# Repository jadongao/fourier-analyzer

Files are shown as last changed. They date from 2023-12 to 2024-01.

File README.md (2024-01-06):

# LEGO Fourier Analyzer
A LEGO machine that presents Fourier Analysis 

GitHub Link: (https://github.com/jadongao/fourier-analyzer)

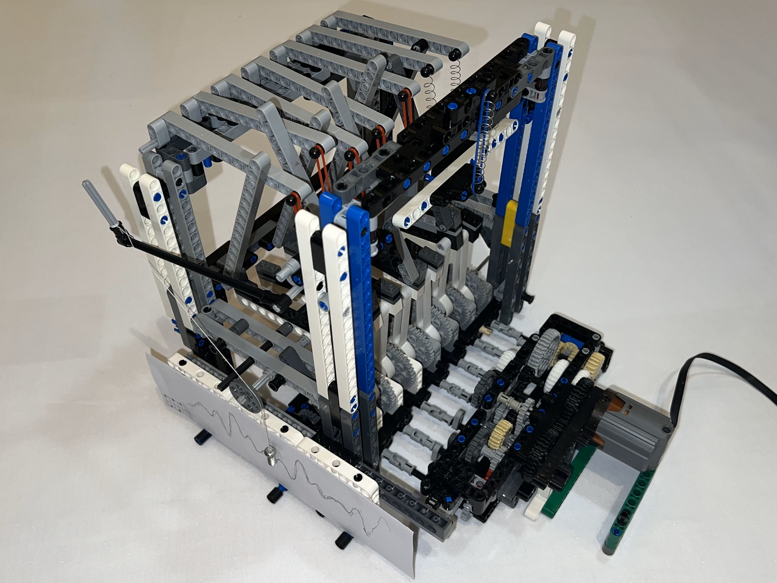
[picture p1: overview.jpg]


# 1. What kind of thing is this work?

I made a LEGO machine that presents Fourier Analysis in a highly visual way. This machine replicates a Harmonic Analyzer designed in the late nineteenth century by the physicist Albert Michelson. I must clarify that I referred to the video of YouTuber @thoroughfareproduction, who created a 5-element analyzer. I redesigned the gearbox to increase the number of elements to 7 and made improvements in the design of the sinusoid generator gear set to make the operation smoother.

# 2. How to characterize/categorize this work?

LEGO machine, Fourier Analysis, Sinusoid, 3D models, Visual Learning

# 3. Briefly description of this work

A Fourier analyzer can carry out two related tasks: add weighted sines or cosines to produce a function graph and perform the inverse operation of decomposing a given function graph into its constituent sinusoids. The addition of sinusoids is called Fourier synthesis, and the inverse operation is called Fourier Analysis. This type of machine is an analog computer that directly processes function graphs without the digital computer, which is almost considered essential by people today. It does not require electricity and can be operated by hand.

The capability of the Fourier analyzer depends on the number of elements. I tried to increase the number of elements to 7, while Albert Michelson's copper analyzer once achieved 80 elements.

## Example of Fourier analysis

Taking Fourier synthesis (5 sinusoids element) as an example,

<!--![sinusoid function graph of computer](./computer%20function%20graph.jpg) -->
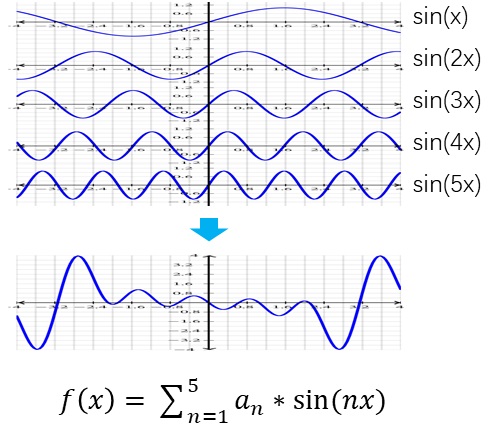
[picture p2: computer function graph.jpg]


where $a_n$ is -1, +1, -1, +1, -1

F (x)= -sin(x)+sin(2x)-sin(3x)+sin(4x)-sin(5x)

Using this LEGO Fourier Analyzer, the output function graph is as follows, which is very close to the graph drawn by the computer.

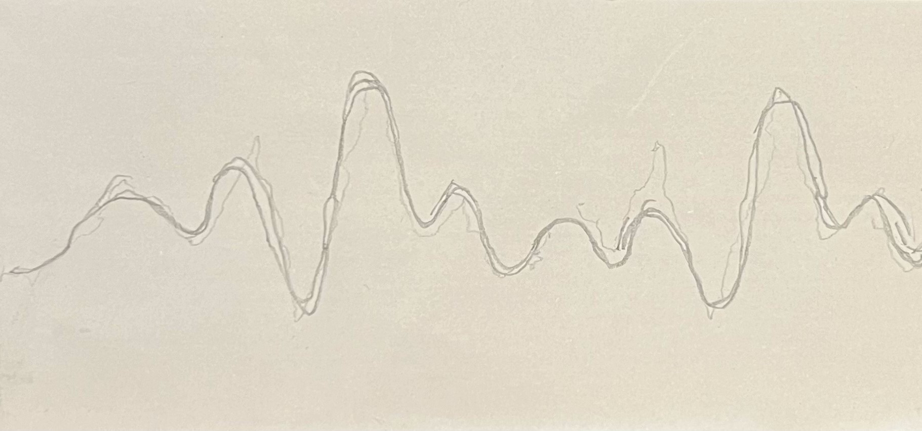
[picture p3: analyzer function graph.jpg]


## Parts of analyzer
This LEGO machine consists of the following parts:

<!--![parts of Analyzer](./overview%20with%20label.jpg)  -->
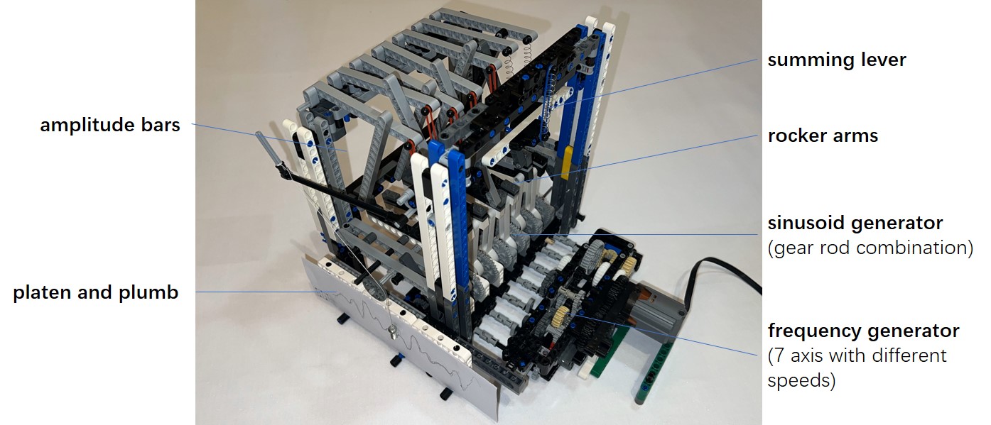
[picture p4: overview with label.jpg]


### 3.1 Frequency generator
The frequency generator is a gearbox with seven output shafts of different frequencies. The rotational speeds on the seven axes are 1x, 2x, 3x, 4x, 5x, 6x, and 7x, respectively.

### 3.2 Sinusoid generator
The sinusoid generator has seven gears to move Rocker arms, converting the circular rotation generated by the frequency generator into sinusoidal motion. This combination of mechanical elements produces the seven different sinusoidal waves: sin(1x), sin(2x), sin(3x), sin(4x), sin(5x), sin(6x), and sin(7x).

### 3.3 Ample bars, weight the sinusoids
There are 7 sinusoidal motions weighted: $a_1$*sin(1x), $a_2$*sin(2x), $a_3$*sin(3x), $a_4$*sin(4x), $a_5$*sin(5x), $a_6$*sin(6x), and $a_7$*sin(7x).
### 3.4 Summing lever
The summing lever at the top of the machine adds together the weighted sinusoids.

### 3.5 Platen and Plumb
The platen moves horizontally, and the plumb moves vertically. The pen tied to the plumb draws a function graph of the calculation result on the recording paper.

# 4. How do I make it?
Since March 2022, I have been in contact with the Harmonic Analyzer, designed by physicist Albert Michelson for studying calculus and Fourier transform, and its clever design has deeply impressed me. So I wanted to make one myself at home. The entire process took considerable time and effort to complete each component.

The sinusoid generator and frequency generator are two essential parts:

### Frequency generator
The frequency generator is a gearbox, and I am amazed by the clever design of Youtuber @thoroughfareproduction. However, because this YouTuber only provided videos without detailed installation drawings, I couldn't see his internal structure and had to explore it myself. I first completed a 5-axis gearbox like a YouTuber's machine, and after finishing it, my confidence doubled. I challenged and assembled a 7-axis gearbox.

<!--![gear set](./frequency%20generator%20gear%20set.jpg) -->
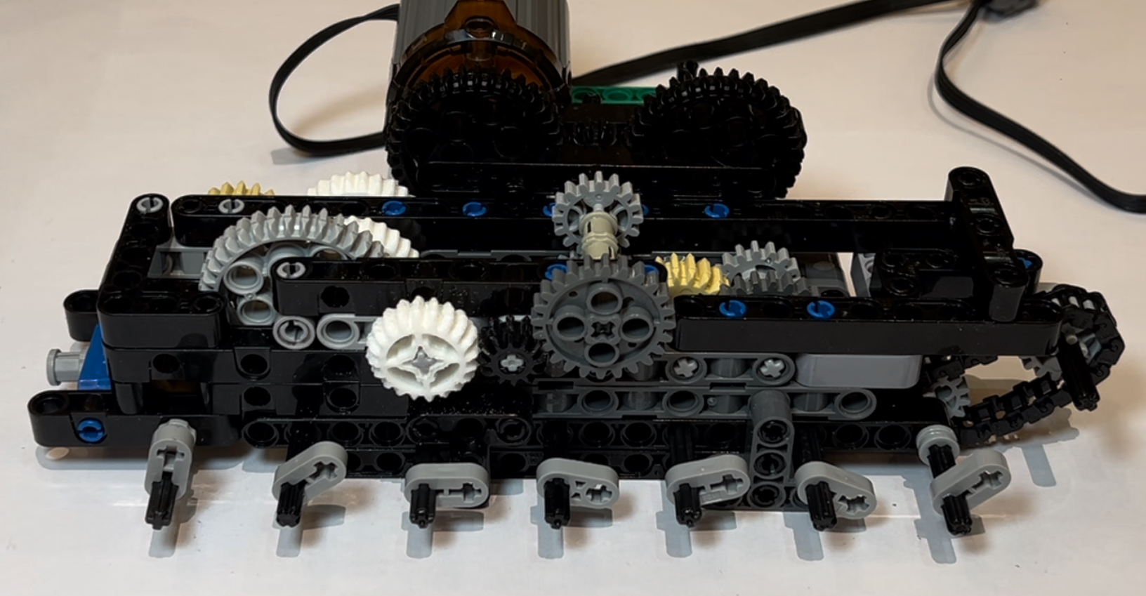
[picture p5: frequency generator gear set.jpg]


This machine uses almost all LEGO gears: 8, 12, 16, 20, 24, 28, and 36 teeth gear. Since I don't have all gear types at home, I temporarily used a 3D printer to print several types. Later, I replaced the 3D-printed parts with purchased LEGO parts, which made the operation more stable. This method of testing before formal procurement dramatically improves production efficiency, eliminating the need to wait several days to receive LEGO parts before testing.

### Sinusoid generator
The sinusoid generator uses LEGO worm gear to transmit circumferential rotation, but during the manufacturing process, there was a problem. Due to the fixed position of the gears and worm, the worm would get stuck during operation, and the entire device could not operate then. I had to take a break until a few months later when I had time to conduct many repeated experiments and finally found a solution. The final method found is straightforward: to make the worm position lose to avoid jamming. But to see this method, I should do many repeated disassembly and assembly. 

The device that drives the LEGO beam to form sinusoidal motion is crucial. Youtuber @thoroughfareproduction used a simple bolt connection, but the bolt connection was loose due to the need for rotation, which caused the gears and beam to shake often. I made improvements using a 3D-printed model and bearings, and it is no longer a classic LEGO work.

<!--![gear-rod and bearing](./gear-rod%20and%20bearing%20with%20label.jpg)-->
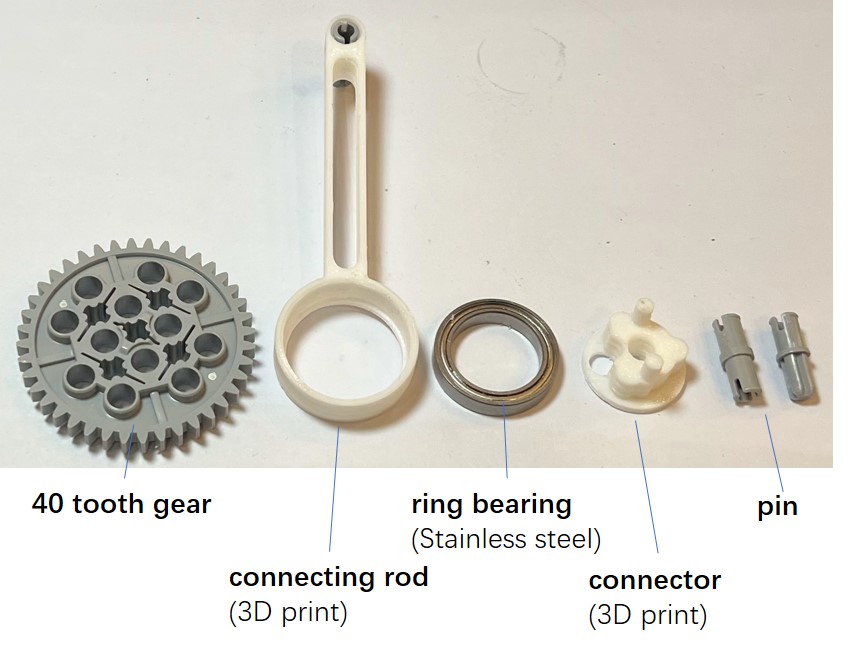
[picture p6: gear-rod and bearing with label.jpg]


<!--![sinusoid generator](./sinusoid%20generator%20gear-rod.jpg) -->
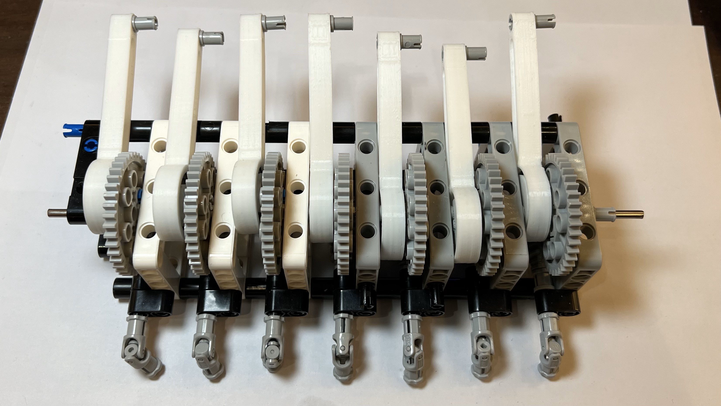
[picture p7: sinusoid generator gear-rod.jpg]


# 5. Why do I make it?

When learning sound waves, I came across the idea that chords are composed of different combinations of sounds, and using Fourier Analysis, chords can be decomposed into the frequencies of their constituent sounds. I am very interested in Fourier Analysis, and I saw videos online from Professor Bill Hammack and YouTuber @thoroughfareproduction, both dedicated to visualizing complex mathematical concepts in Fourier Analysis. So, I decided to learn from them and make a LEGO machine myself. When making this machine, I also traced the history of Fourier Analysis. I had a chance to communicate with these masters during this production process, and I felt their imaginative ideas in the era without electronic computers.

<table border="0">
 <tr>
    <td><b style="font-size:30px">Time</b></td>
    <td><b style="font-size:30px">Name</b></td>
    <td><b style="font-size:30px">Invention</b></td>
 </tr>
 <tr>
    <td>1807</td>
    <td>French mathematician and physicist Fourier </td>
    <td>He published a paper that used sine curves to describe temperature distribution: periodic functions can be represented by a series of cosines and sines.</td>
 </tr>
<tr>
    <td>1879</td>
    <td>Sir William Thomson (Lord Kelvin)</td>
    <td>He designed a 15 constituent sinusoids tide predicting machine (TPM). </td>
</tr>
<tr>
    <td>1898</td>
    <td>Physicist Albert Michelson (Nobel Prize Winner) </td>
    <td>He designed the Harmonic Analyzer that calculates with 20 sinusoids. </td>
</tr>
<tr>
    <td>November 12, 2014</td>
    <td>Professor Bill Hammack </td>
    <td>He uses videos and PDF books to introduce Albert Michelson's Harmonic Analyzer. </td>
</tr>
<tr>
    <td>August 19, 2021</td>
    <td>Youtuber @thoroughfareproduction </td>
    <td>They designed a wondrous LEGO contraption of gears, springs, levers, and wheels to perform Fourier analysis. </td>
</tr>
</table>

# 6. What's the most meaningful thing you've made?

This LEGO machine can correspond one-to-one with mathematical formulas, which visualizes mathematical concepts and helps me understand them.

<!--![sinusoid generator](./math%20to%20machine.jpg)-->
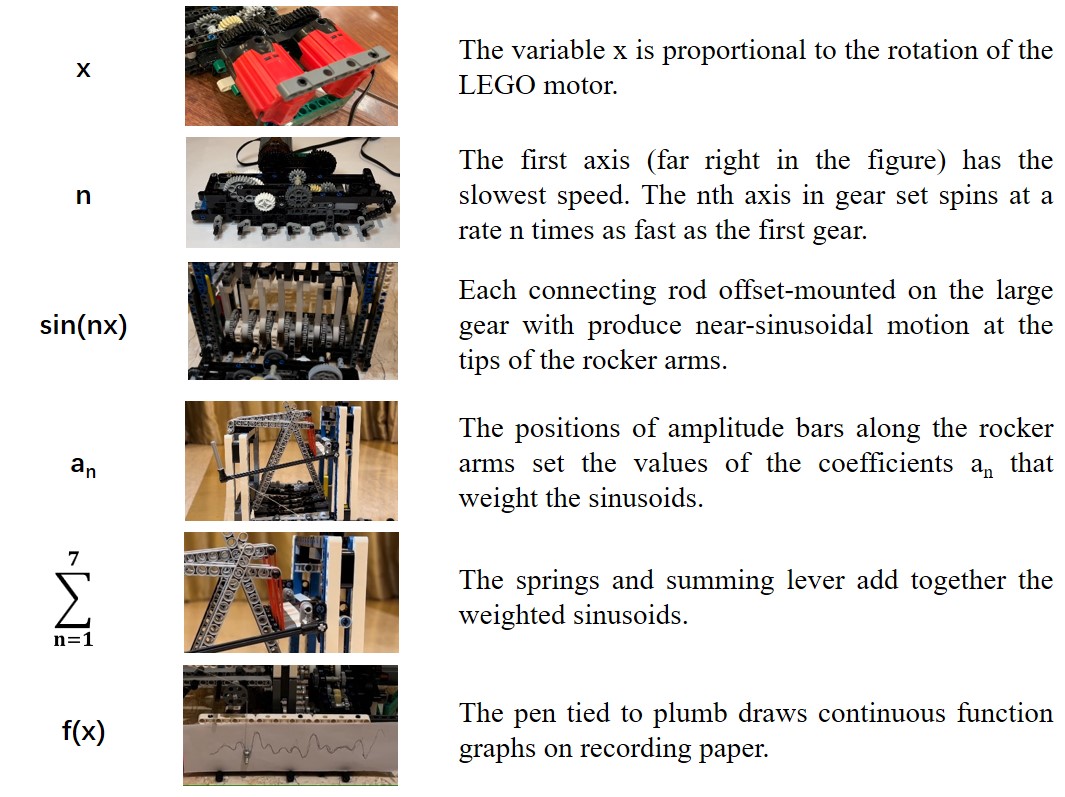
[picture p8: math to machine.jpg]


The production process of this machine was a perfect visual learning. It's very consistent with my experience as a tutor in a schoolhouse. The visual teaching method enables students to see and touch the abstract concepts they have learned, bringing students (including myself) closer to the abstract concepts.

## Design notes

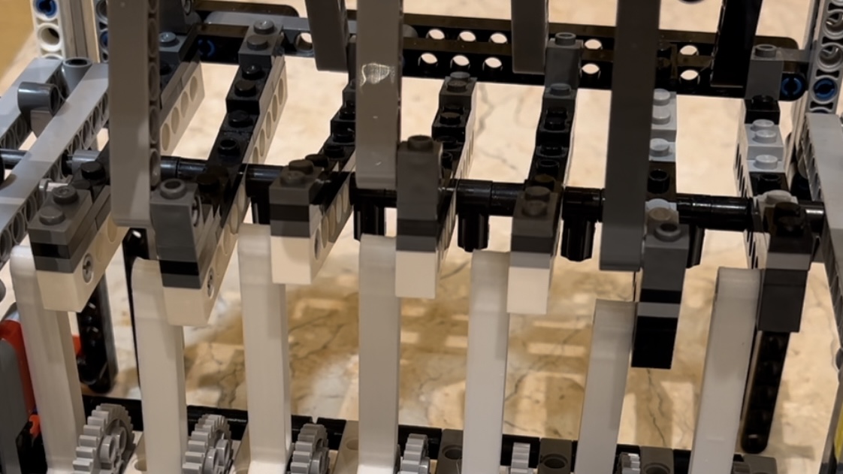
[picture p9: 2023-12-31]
rocker arm.jpg

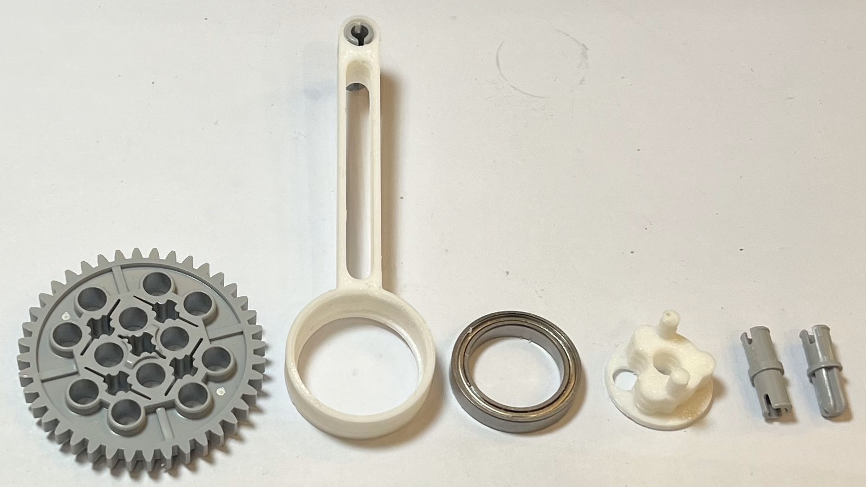
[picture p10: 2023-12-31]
rod gear and bearing.jpg

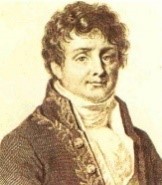
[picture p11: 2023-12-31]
Fourier.jpg

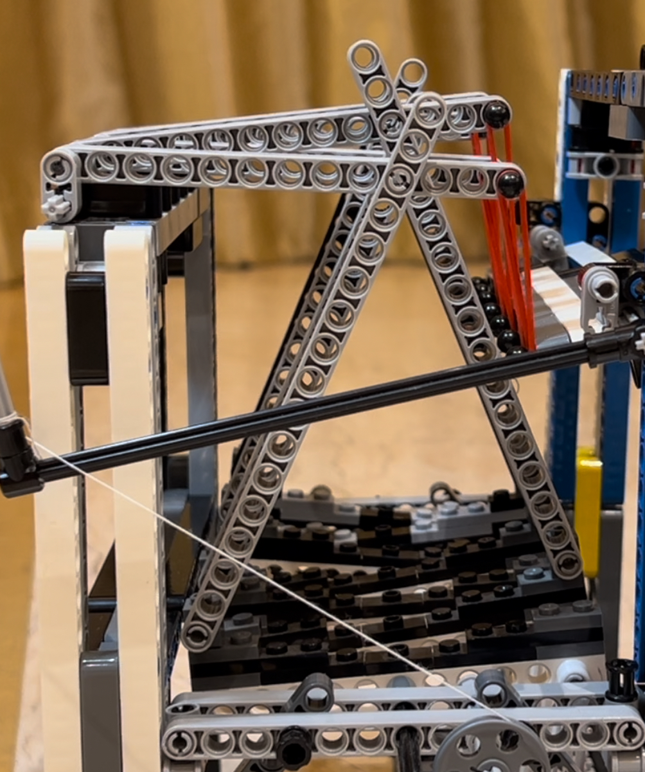
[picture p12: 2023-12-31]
amplitude bar.jpg

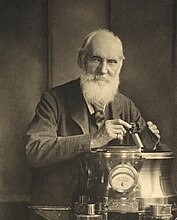
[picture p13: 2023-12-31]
Lord Kelvin.jpg

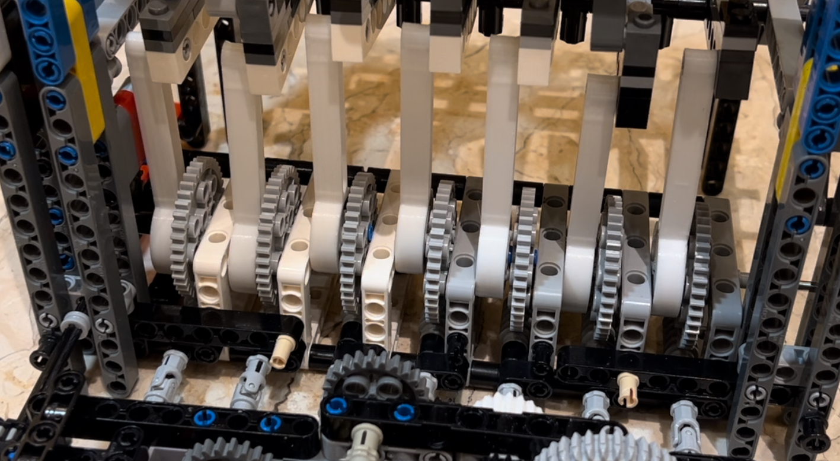
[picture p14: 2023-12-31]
sinusoid generator.jpg

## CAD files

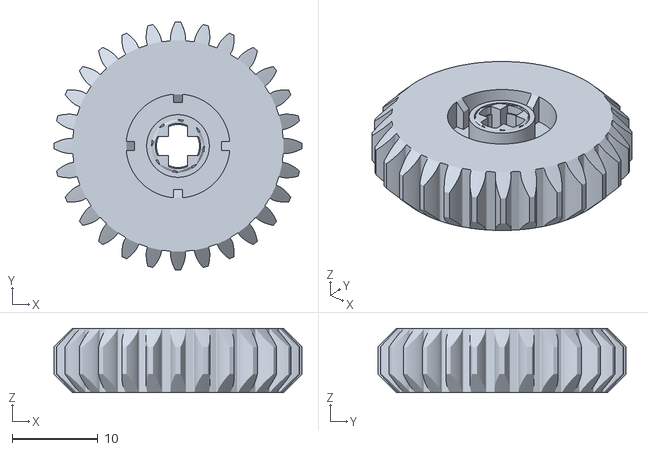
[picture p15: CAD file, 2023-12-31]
Gear28.stl
28.9 x 28.9 x 7.50

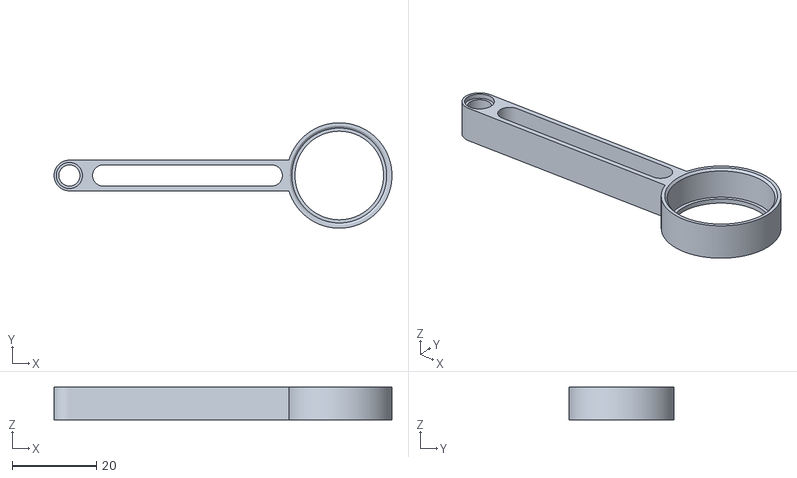
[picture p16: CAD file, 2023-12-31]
Rod.stl
80.2 x 25.0 x 7.80

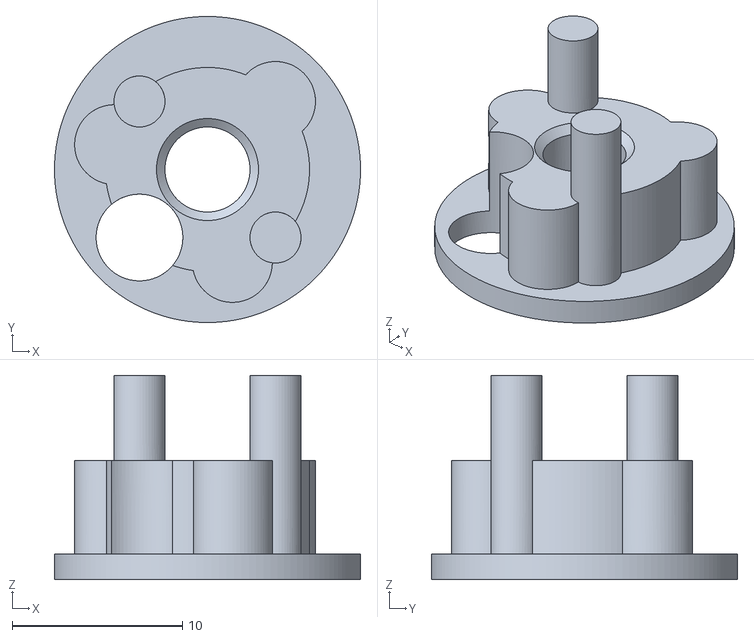
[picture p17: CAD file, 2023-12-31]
connector.stl
18.0 x 18.0 x 12.0

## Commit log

2023-12-31 Rename 2023-12-31 005647.jpg to frequency generator gear set.jpg
2023-12-31 Rename 2023-12-31 015705.jpg to rocker arm.jpg
